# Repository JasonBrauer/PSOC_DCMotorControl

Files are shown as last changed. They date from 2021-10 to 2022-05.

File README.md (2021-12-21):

# Motor_Control_Experiment
Experiment to implement a motor controller from a Cypress Semiconductor PSOC5 and basic electrical components

## Current_Circuit_Design
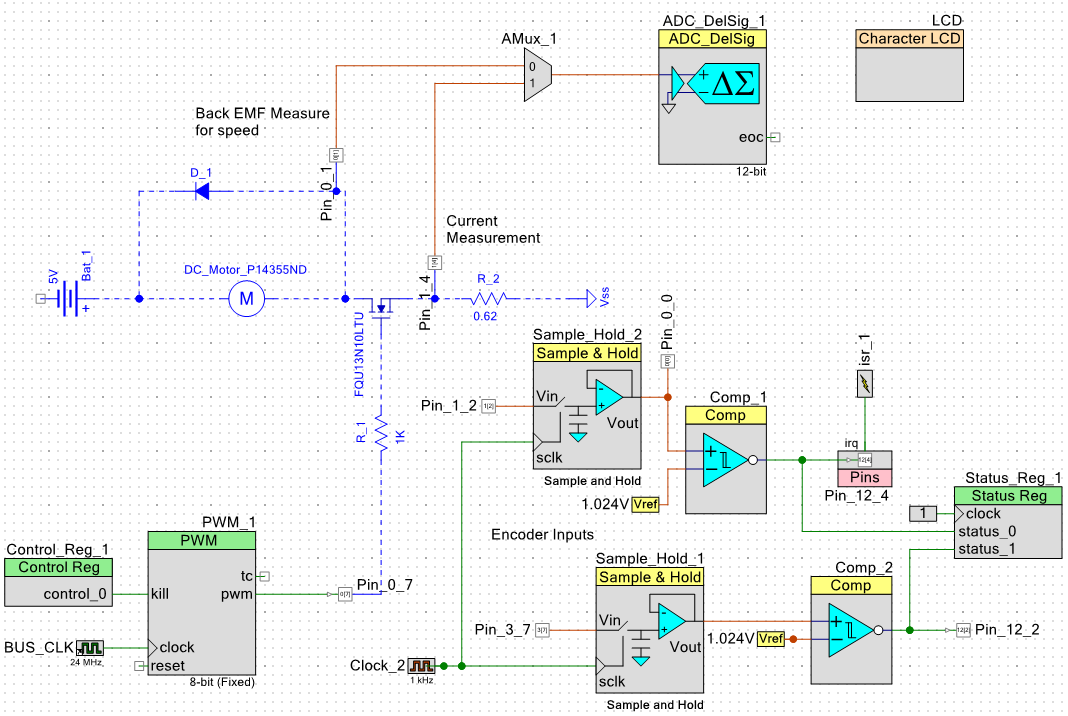
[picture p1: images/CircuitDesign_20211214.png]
current circuit


## Speed_From_BackEmf
A simple motor can be thought of as an inductor, resistor and back emf voltage source all in series. The voltages from the inductor, resistor, and back emf all oppose the supplied voltage to the motor:

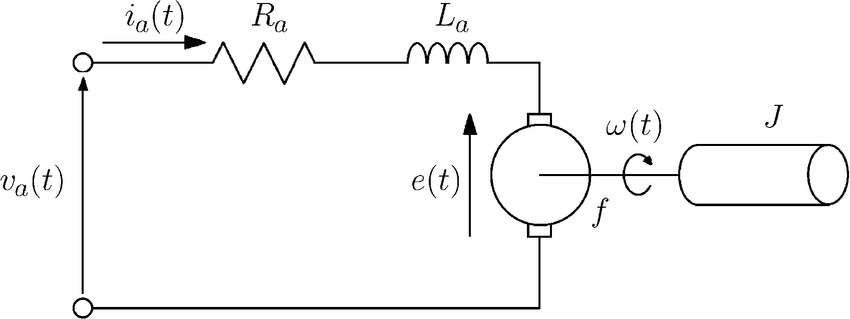
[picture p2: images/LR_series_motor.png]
LR series


source: https://www.researchgate.net/figure/Equivalent-circuit-of-an-armature-controlled-dc-motor_fig1_3050910

V_supply - V_L - V_R - V_bemf = 0

The opposing voltage of the inductor is due to a varying current in time:

V_L = L * dI/dt 

Once the current reaches steady state, di/dt becomes zero and therefore V_L becomes zero. The current is dissipated via the resistance R in the RL circuit. Back emf is based only on motor speed. Therefore it can be measured directly once the voltage generated by the inductance of the motor is fully dissipated - after ~5 L/R time constants. 

The equation for voltage an RL series circuit without considering the back emf is:

V_supply - V_L - V_R = 0

Substituting V_R = IR and V_L = L* di/dt, the equation becomes:

V_supply = IR + L * dI/dt, which can be solved for the current (I) via integration and substitution. Current for the series RL circuit then becomes:

I = V_supply/R * (1 - e^(-Rt/L))

We can then plug the equation for current into V_L = L * dI/dt to find V_L in terms of V_supply, R and L - which resolves to:

V_L = V_supply * e^(-Rt/L) 

The voltage settling time for the P14355ND motor currently used the experiment is ~100 microseconds. Therefore the code waits 200 microseconds to allow some additional buffer before taking the voltage reading for back emf. We could use the measured settling time to determine L assuming we measure R and knowledge that settling time is equal to 5 L/R time constants. 

L = t_settling * R / 5

```C
/**
*Calculates back emf in mV using supply voltage as a reference
*@param v_supply_mv int16 voltage supplied to the motor
*
*returns back_emf_mv int16 back emf voltage in mv
*/
static int16 read_back_emf(int16 v_supply_mv){
    Control_Reg_1_Write(1);
    CyDelayUs(200);
    AMux_1_Select(0);
    ADC_DelSig_1_StartConvert();
    ADC_DelSig_1_IsEndConversion(ADC_DelSig_1_WAIT_FOR_RESULT);
    CyDelayUs(5); // add delay for conversion to complete
    Control_Reg_1_Write(0);
    int32 back_emf_counts = (int32)ADC_DelSig_1_GetResult16();
    return(v_supply_mv - ADC_DelSig_1_CountsTo_mVolts(back_emf_counts));
}
```

The following readout from the oscilliscope at the location of Pin_0_1 is at a time scale of 100 microseconds per division:
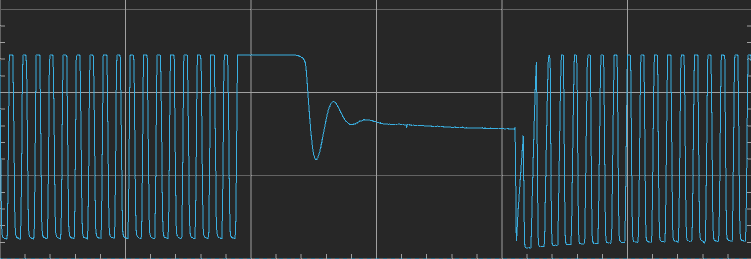
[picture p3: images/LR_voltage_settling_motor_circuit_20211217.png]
LR Settling


The voltage drop across the resistance of the motor also only applies when current is flowing:

V_R = I * R

The ground path from the motor can be removed to assist in measuring the back emf. This will cause a short voltage and current spike as the inductance of the motor will oppose the sudden drop in current from the voltage supply. A flyback diode will allow the current from the motor inductance to safely dissipate.

Waiting long enough for the current to dissipate and reach steady state allows the measured voltage of the circuit become:

V_supply - V_bemf = V_measured

V_bemf = V_measured - V_supply

The external voltage needs to be considered as it is still connected to the motor circuit even after the ground path is removed.

Then the speed constant of the motor (Ke) can be used in combination with the back emf voltage to calculate the speed. 

motor_speed = V_bemf / K_e

K_e is a constant property of the motor based on its winding design and is typically included in the motor spec. In an ideal motor where L=0, R=0 and no mechanical losses occur, K_e will be equal to the supplied motor voltage over the max rotational speed in a no-load state. That is because in the ideal scenario, the back emf would be the only opposition to the supply voltage and the only thing limiting the motor's speed.

## Manual_Rotary_Encoder
Inputs read with comparators to convert analog signals from the encoder to digital signals for use in the controller.

Sample and hold devices used with 1kHz sample rate to filter out high frequency analog noise generated by the mechanical contacts within the encoder.

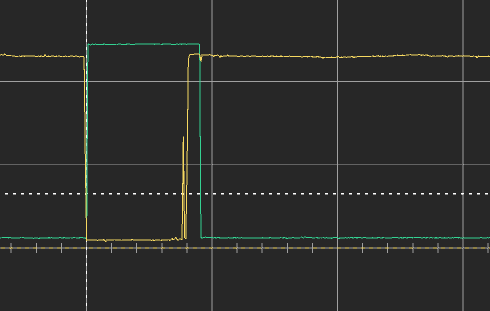
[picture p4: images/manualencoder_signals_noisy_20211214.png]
manual encoder signals noisy


### Issues
At a frequency of about 1/10 notches, reading the encoder registers a positive increment instead of negative when rotating CCW. Haven't determined the source of the problem, but it could be because the falling edge of the 'lead' signal occurs at nearly the same instant or possible even behind the trailing signal.The interrupt service routine that sample the encoder signals triggers on the falling edge of the red signal below.

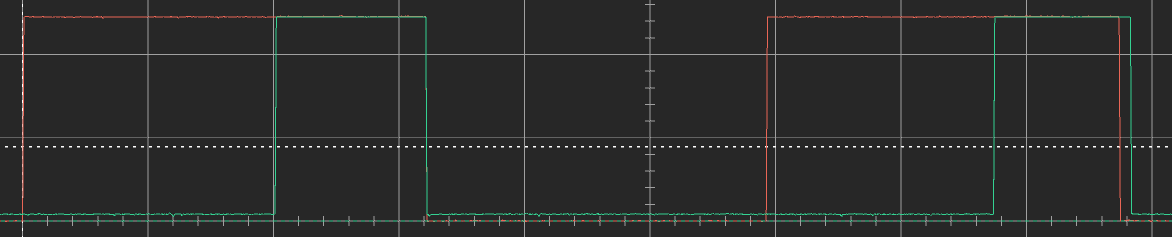
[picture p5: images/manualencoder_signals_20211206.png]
manual encoder signals


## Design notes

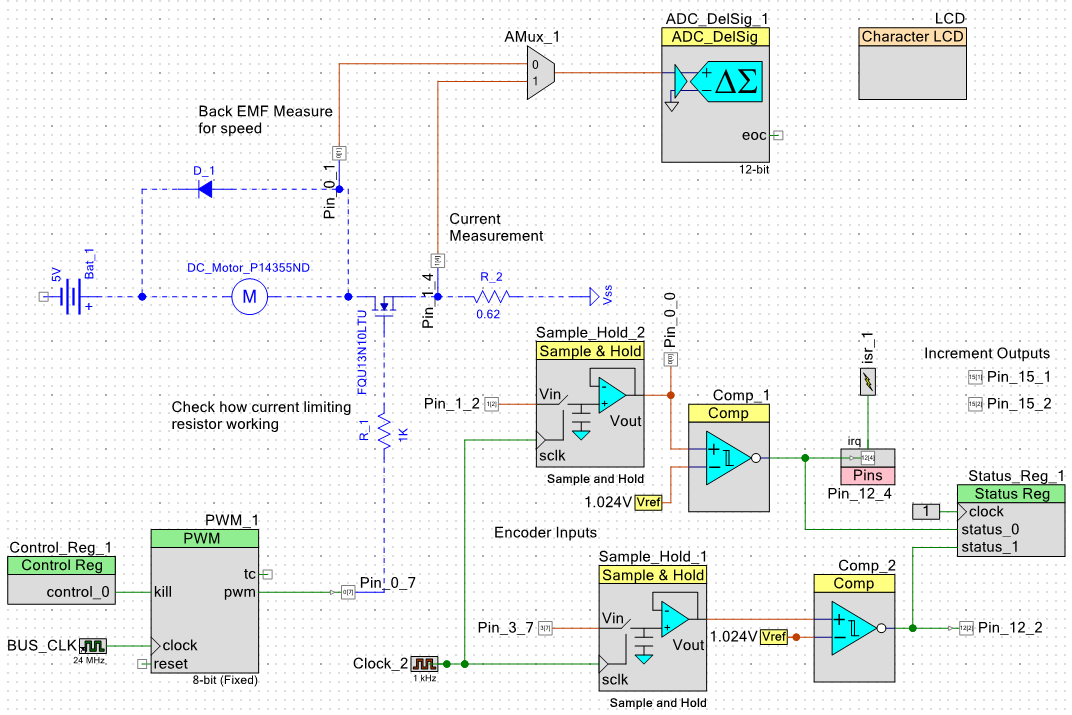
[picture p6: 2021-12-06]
images/CircuitDesign_20211206.png

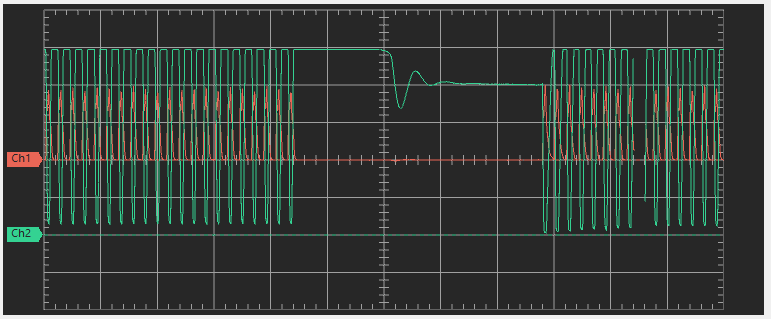
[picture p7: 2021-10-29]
images/backemf_voltplot_lowspeed.png

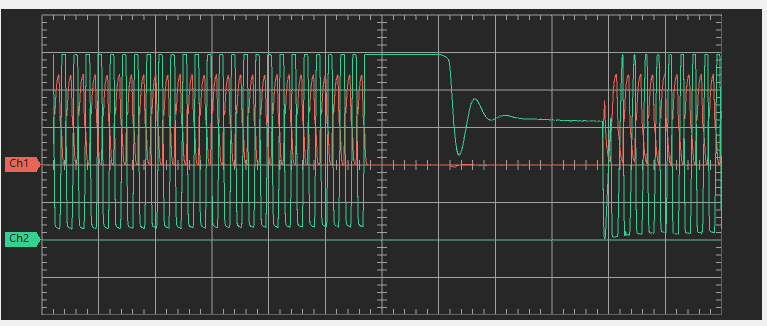
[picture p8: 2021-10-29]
images/backemf_voltplot_highspeed.png

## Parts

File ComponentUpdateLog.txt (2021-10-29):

Last Modified Date & Time: 10/26/2020 18:24:53

DCMotorControl: DCMotorControl.cydwr
	cy_boot [v5.70] to [v5.81]
	Em_EEPROM_Dynamic [v2.0] to [v2.20]
	LIN_Dynamic [v4.0] to [v5.0]

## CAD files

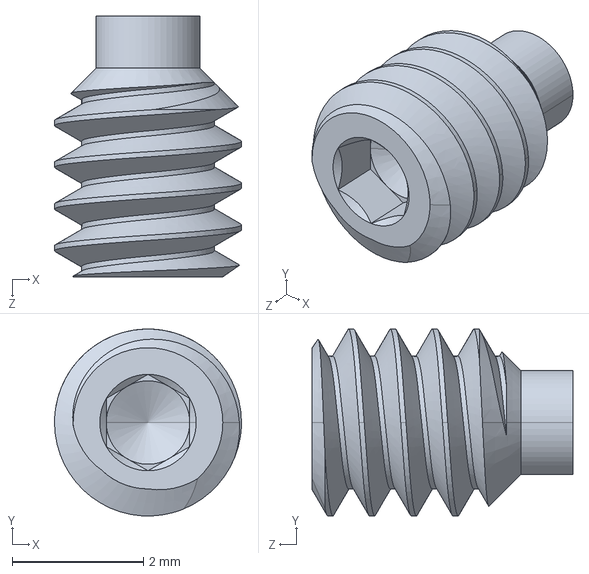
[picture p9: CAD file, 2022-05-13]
cad/90291A103_set _screw.STEP
2.84 x 2.84 x 3.97 mm

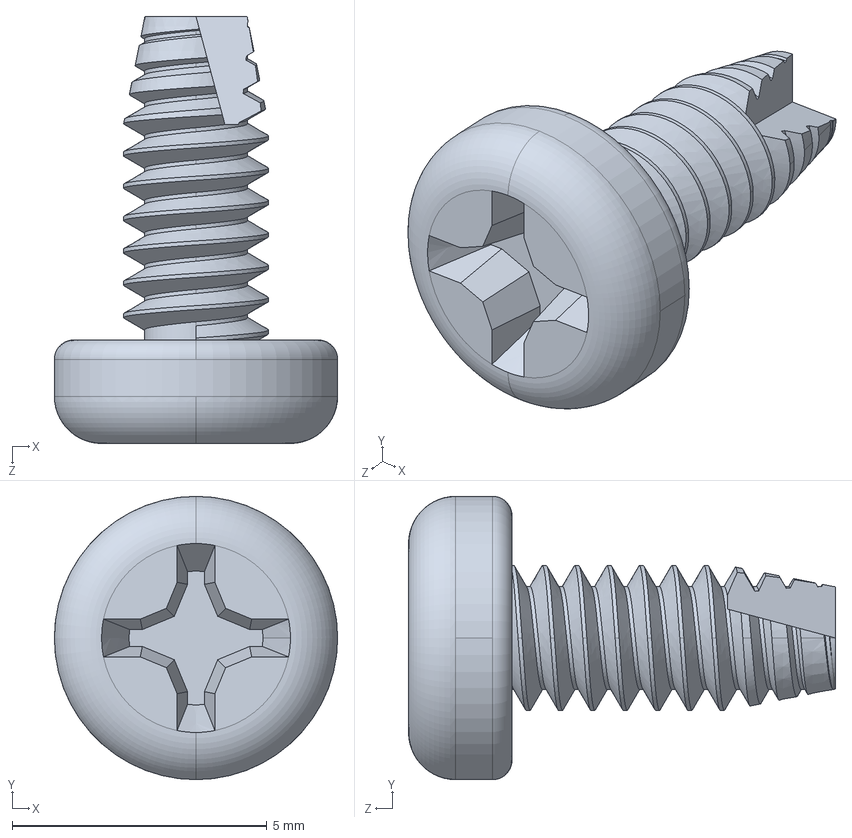
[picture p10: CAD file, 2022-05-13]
cad/98273A110_thread_cutting_screw.STEP
5.56 x 5.56 x 8.38 mm

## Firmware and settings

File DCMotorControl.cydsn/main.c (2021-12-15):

/* ========================================
 *
 * Copyright YOUR COMPANY, THE YEAR
 * All Rights Reserved
 * UNPUBLISHED, LICENSED SOFTWARE.
 *
 * CONFIDENTIAL AND PROPRIETARY INFORMATION
 * WHICH IS THE PROPERTY OF your company.
 *
 * ========================================
*/
#include "project.h"
#include "dcmotor.h"
#include "rotaryencoder.h"

/* Global variables */
volatile int input_speed = 0;

/* Functions  */
static int16 read_back_emf(int16);

/**
*PSOC specific macro that wraps an Interrupt Service Routine function
*endcoder_interrupt is the ISR used to read a rotary encoder input
*@param encoder_interrupt (interrupt function name)
*
*/
CY_ISR(encoder_interrupt)
{
    uint8 encoder_status;
    // encoder_status reading as 0 or 2 instead of expected 1 or 3
    encoder_status = Status_Reg_1_Read();
    int increment = readEncoder((int)encoder_status);
    input_speed = adjustSpeed(input_speed, increment);
    Pin_12_4_ClearInterrupt();
}


int main(void)
{
    CyGlobalIntEnable; /* Enable global interrupts. */

    /* Place your initialization/startup code here (e.g. MyInst_Start()) */
    PWM_1_Start();
    AMux_1_Start();
    ADC_DelSig_1_Start();
    LCD_Start();
    Comp_1_Start();
    Comp_2_Start();
    Comp_1_ZeroCal();
    Comp_2_ZeroCal();
    Sample_Hold_1_Start();
    Sample_Hold_2_Start();
    isr_1_StartEx(encoder_interrupt);
    
    
    int16 v_supply_mv = 4500;
    int delay_count = 0;

    while(1)
    {   
        delay_count++;
        PWM_1_WriteCompare(input_speed);
        
        CyDelay(1); // Delay 1 millisecond
        /* Calc speed between each delay request */
        int16 back_emf_mv = read_back_emf(v_supply_mv);

        /* only write to LCD every 100 loops (100 ms) */
        if(delay_count % 500 == 0) {
            LCD_Position(0,0);
            //              -0123456789012345- 16 char guide
            LCD_PrintString("speed_rpm:        ");
            LCD_Position(0,10);
            LCD_PrintNumber((uint16)speedFromBackEmf((int)back_emf_mv, 0.3466));
            
            LCD_Position(1,0);
            //              -0123456789012345- 16 char guide
            
            LCD_PrintString("input_speed:        ");
            LCD_Position(1,13);
            LCD_PrintNumber((uint16)input_speed);
        }
    }
}


/**
*Calculates back emf in mV using supply voltage as a reference
*@param v_supply_mv int16 voltage supplied to the motor
*
*returns back_emf_mv int16 back emf voltage in mv
*/
static int16 read_back_emf(int16 v_supply_mv){
    Control_Reg_1_Write(1);
    CyDelayUs(200);
    AMux_1_Select(0);
    ADC_DelSig_1_StartConvert();
    ADC_DelSig_1_IsEndConversion(ADC_DelSig_1_WAIT_FOR_RESULT);
    CyDelayUs(5); // add delay for conversion to complete
    Control_Reg_1_Write(0);
    int32 back_emf_counts = (int32)ADC_DelSig_1_GetResult16();
    return(v_supply_mv - ADC_DelSig_1_CountsTo_mVolts(back_emf_counts));
}
/* [] END OF FILE */

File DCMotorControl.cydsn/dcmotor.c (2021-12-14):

/* ========================================
 *
 * Copyright YOUR COMPANY, THE YEAR
 * All Rights Reserved
 * UNPUBLISHED, LICENSED SOFTWARE.
 *
 * CONFIDENTIAL AND PROPRIETARY INFORMATION
 * WHICH IS THE PROPERTY OF your company.
 *
 * ========================================
*/
#include "dcmotor.h"

/**
*Calculates the motor speed in rpm from back Emf and the motor speed constant
*@param backEmf an integer of the back emf in mV
*@param motorSpeedConstant a float of the motor speed constant in (mV / min^-1)
*
*returns integer speed in rpm
*/
int speedFromBackEmf(int backEmf, float motorSpeedConstant) 
{
    return((int)(backEmf / motorSpeedConstant)); 
};

/* [] END OF FILE */

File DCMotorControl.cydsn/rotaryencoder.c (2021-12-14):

/* ========================================
 *
 * Copyright YOUR COMPANY, THE YEAR
 * All Rights Reserved
 * UNPUBLISHED, LICENSED SOFTWARE.
 *
 * CONFIDENTIAL AND PROPRIETARY INFORMATION
 * WHICH IS THE PROPERTY OF your company.
 *
 * ========================================
*/
#include "rotaryencoder.h"
#include "string.h"

struct Output {
    int count;
    char direction[5];
};


/**
*Determines an encrement based on a register value read from a rotary encoder
*@param register_value an integer of a status register value
*
*returns increment integer value of the increment 
*    either: -1, 1, 0 (default)
*/
int readEncoder(int register_value)
{
    int increment = 0;
    if(register_value == 0) {
        increment = 1;
    }
        
    if(register_value == 2) {
        increment = -1;
    }
   
    return(increment);
    
};

/**
*Adjusts an 8-bit period value for use with a PWM output driving motor speed
*@param speed integer current 8-bit period value
*@param increment integer -1, 1, 0 increment multiplier (multiplier is 5)
*
*returns speed new integer value for the 8-bit period 
*    either: -1, 1, 0 (default)
*/
int adjustSpeed(int speed, int increment)
{
    //int speed_increment = increment * 5;
    
    if(speed <= 250 && speed >= 5) {
        //speed = speed + speed_increment;
        if(increment == -1) {
            speed = speed - 5;
        }
        if (increment == 1) {
            speed = speed + 5;
        }
        return(speed);
    }
        
    if(speed > 250 && increment < 0) {
        speed = speed - 5;
        return(speed);
    }
    
    if(speed < 5 && increment > 0) {
        // speed = speed + speed_increment;
        speed = speed + 5;
        return(speed);
    }

    return(speed);

};
/* [] END OF FILE */

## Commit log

2020-08-31 initial schematic
2020-09-14 add AMux and ADC
2020-09-14 configure ADC
2020-09-14 configure pin 7 for external input
2020-09-14 hook up ADC
2020-10-17 motor toggle on / off 5 / 3 sec
2020-10-17 initial pwm setup
2020-10-18 speed scaling pwm signal
2020-10-27 print mv to display
2020-10-27 fix brackets
2020-10-29 control register logic to shut off pwm
2020-10-29 comment out long motor delay
2020-10-30 voltage displays but too high
    [main.c]
2020-11-14 using isendconversion for ADC
2021-04-01 digital pin inputs
2021-04-01 configure encoder digital in pins
2021-04-01 stub encoder functions
2021-06-23 add encoder input via comparator
2021-06-25 add analog taps for encoder inputs
2021-09-27 swap input pin for encoder
2021-09-28 sample and hold one encoder channel
2021-09-30 comp digital read of encoder inputs
2021-10-08 interrupt read failing
2021-10-13 rotary inputs read and print but bad results
2021-10-20 adjust encoder read logic and data types
2021-11-30 successful isr from digital input output pin
2021-12-06 filter high freq noise with sample and hold
    [main.c]
2021-12-06 print input speed to screen
2021-12-06 discuss current manual encoder issues in readme
2021-12-06 ref to circuit design image in readme
2021-12-07 remove troubleshooting code and use rotary encoder speed
2021-12-13 fix input guard on dcmotor header
    [dcmotor.c, main.c]
2021-12-14 update circuit diagram pic
2021-12-14 noisy rotary encoder signal image in readme
2021-12-15 back emf voltage calc into sep function
2021-12-21 v_l calc and motor circuit image
2022-05-13 motor test stand cad models
    [90291A103_set _screw.STEP, 98273A110_thread_cutting_screw.STEP]
